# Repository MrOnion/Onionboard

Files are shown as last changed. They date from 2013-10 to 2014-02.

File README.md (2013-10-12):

# Onionboard PCB for FreeEMS

This PCB is intended to be used in conjunction with a separate microcontroller module to create a basic engine management system. It has a simple power supply and enough general purpose I/O to get started. Basically any microcontroller and software combo can be used but it is particulary designed to be used with the open-source FreeEMS project.

http://freeems.org/

Its ideal for people who wants to experiment and learn about the world of engine management.

The project is done with CadSoft Eagle version 6.x and is kept within the freeware limitations.

http://www.cadsoftusa.com/download-eagle/freeware/

## Features

* 2-Layer PCB
* Size is about 10x10cm (fits in a euro case)
* 5V LDO regulated power supply with VDR protection
* 2 Polyfuse protected 5V reference voltage outputs
* 4 auto-protected injector outputs (high impedance only)
* 2 auto-protected accessory outputs
* 4 mosfet drivers for ignition amplifiers (5V or 12V)
* 4 protected A/D inputs
* 4 protected temperature inputs (can be used as normal A/D)
* 2 protected on/off switch inputs
* 2 ground loop monitor inputs
* CEL LED and run/load switch for FreeEMS

One thing to point out is that at this stage the board DOES NOT have VR/Hall sensor inputs. As these sensors are mandatory to operate an EMS there are pin headers/DIP8 socket and places for shunt resistors (used with VR) to be used with a separate BrickRPM VR conditioner board. More info at: http://brickems.com/brickrpm/

## Notes

The schematic and board file both have a placeholder for git commit id. This is used with the git clean/smudge filter. The .gitattributes file is included with the project but it only defines the files to be filtered with a filter called "hasher". You can use this feature by adding this into your .git/config file:
```
[filter "hasher"]
        smudge = sed \"s/GIT %GIT_COMMIT_ID%/GIT `git rev-parse --verify HEAD --short`/\"
        clean = sed \"s/GIT [0-9a-z]\\{7\\}/GIT %GIT_COMMIT_ID%/\"
```
As you can see this is OS specific and works straight in Linux and OSX.

The filter has one downside which is the need to make an extra deletion and checkout for the id to be "smudged". For example if you clone this project the git placeholder don't have the current id. You need to delete the files and checkout them for the id to be updated:

```
$ rm onionboard.sch onionboard.brd 
$ git checkout onionboard.sch onionboard.brd
```

The project uses a separate Molex connector library I found here:
https://code.google.com/p/rdubniewski-test/source/browse/trunk/eagle.lib/con-molex-5569.lbr
It's also included in the libs directory.

If you decide to home etch this pcb I recommend to make the vias larger (the copper area) before doing so. This way its easier to drill them and solder the connecting wire.

Heres a good tip for home made vias:
http://www.youritronics.com/double-layer-pcb-home-made-vias/

## TODO

* Get more testing done and lots of driving/racing.
* Possibly put a dual VR conditioner on board (MAX992x based)
* Also one H-bridge driver would be ideal

## CPU Modules used with FreeEMS (MC9S12XDP512)

* **TA Adapt9S12XDP512** - http://www.technologicalarts.ca/shop/store/details/453/11/microcontrollers/adapt9s12xdp512m2-xgate-mcu-module,-full-configuration.html
* **ElMicro CardS12** - http://elmicro.com/en/cards12.html
* **WayEngineer MC9S12XDP512-core** - http://www.wayengineer.com/index.php?main_page=product_info&products_id=281

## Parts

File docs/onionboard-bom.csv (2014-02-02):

Qty | Value | Package | Parts | Description
1 |  | 1X02 | JP1 | Through-hole pin header (VR1/2 Out)
2 |  | 1X04 | JP6, JP7 | Through-hole pin header (BrickRPM)
48 |  | SMD1,27-2,54 | ACC1, ACC2, ACCMON, AD1, AD2, AD3, AD4, ADB1, ADB2, ADB3, ADB4, BRV, CEL+, CEL-, IGN1, IGN2, IGN3, IGN4, INJ1, INJ2, INJ3, INJ4, INJMON, LD_RUN1, LD_RUN2, PA6, PAD3, PAD4, PAD5, PAD6, PAD7, PAD8, PAD13, PAD14, PAD17, PAD18, PAD19, PAD20, PAD21, PAD22, PAD27, PAD28, PAD29, PAD30, PAD35, PAD36, SW1, SW2 | SMD pin headers (pin count)
4 | 1uF | C0805 | C1, C3, C5, C7 | CAPACITOR, A/D bias inputs
9 | 0.1uF | C0805 | C2, C4, C6, C8, C14, C16, C18, C20, C22 | CAPACITOR, A/D channels
2 | 0.1uF | C1206 | C11, C12 | CAPACITOR, Power supply
5 | 0.22uF | C0805 | C13, C15, C17, C19, C21 | CAPACITOR, A/D non-biased inputs
2 | 15nF | C0805 | C23, C24 | CAPACITOR, GND monitors
2 | 1uF | C1206 | C25, C26 | CAPACITOR, MOSFET drivers
1 | 10uF | SMC_E | C9 | POLARIZED CAPACITOR, Power supply
1 | 47uF | SMC_E | C10 | POLARIZED CAPACITOR, Power supply
2 | 5k | 411 | R6, R8 | RESISTOR, Shunt
4 | 100R | 411 | R52, R53, R54, R55 | RESISTOR, Current limit
11 | 470R | R1206 | R1, R3, R4, R5, R11, R13, R14, R15, R44, R50, R51 | RESISTOR, A/D channels
10 | 100k | M0805 | R22, R24, R26, R28, R30, R32, R37, R38, R39, R40 | RESISTOR, Output pulldown
13 | 1k | M0805 | R21, R23, R25, R27, R29, R31, R33, R34, R35, R36, R46, R47, R48 | RESISTOR, Output limit, BRV, CEL/Load
4 | 1k | R0805 | R9, R10, R56, R57 | RESISTOR, BrickRPM hall mod
4 | 1k | R1206 | R16, R18, R19, R20 | RESISTOR, Switch inputs
4 | 2.49k | M0805 | R2, R7, R12, R17 | RESISTOR, A/D Bias
1 | 3.9k | M0805 | R45 | RESISTOR, BRV
1 | 2.4k | M0805 | R49 | RESISTOR, CEL
1 | 5.1V | P1Z12 | D9 | Z-Diode, Power supply
2 | 4.7V | SOT23 | D13, D14 | Z-Diode, Switch inputs
13 | BAT54S | SOT23 | D1, D2, D3, D4, D5, D6, D7, D8, D10, D11, D12, D15, D16 | Schottky Diodes, A/D channels
1 | 22-27-2041-04 | 6410-04 | J1 | CONNECTOR Molex, Power supply
2 | 5569-6 | 5569-6 | X2, X3 | 4.20mm Pitch Mini-Fit Jr.™ - 6 pin
1 | 5569-8 | 5569-8 | X1 | 4.20mm Pitch Mini-Fit Jr.™ - 8 pin
1 | D0A-L | D02A-L | KK1 | HEATSINK
1 | LM2940 | 78XXL | IC3 | VOLTAGE REGULATOR
2 | RXE030 | RXE030 | R42, R43 | POLYFUSE, Vref outputs
1 | S14K11 | S14K11 | R41 | VARISTOR, Power supply
2 | TC442xA | SO08 | IC1, IC2 | Dual High-Speed Power MOSFET Drivers
6 | VND14NV04 | TO252 (DPAK) | Q1, Q2, Q3, Q4, Q5, Q6 | Fully autoprotected Power MOSFET

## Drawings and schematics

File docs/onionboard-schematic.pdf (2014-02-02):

### ABCDE

### ABCDE

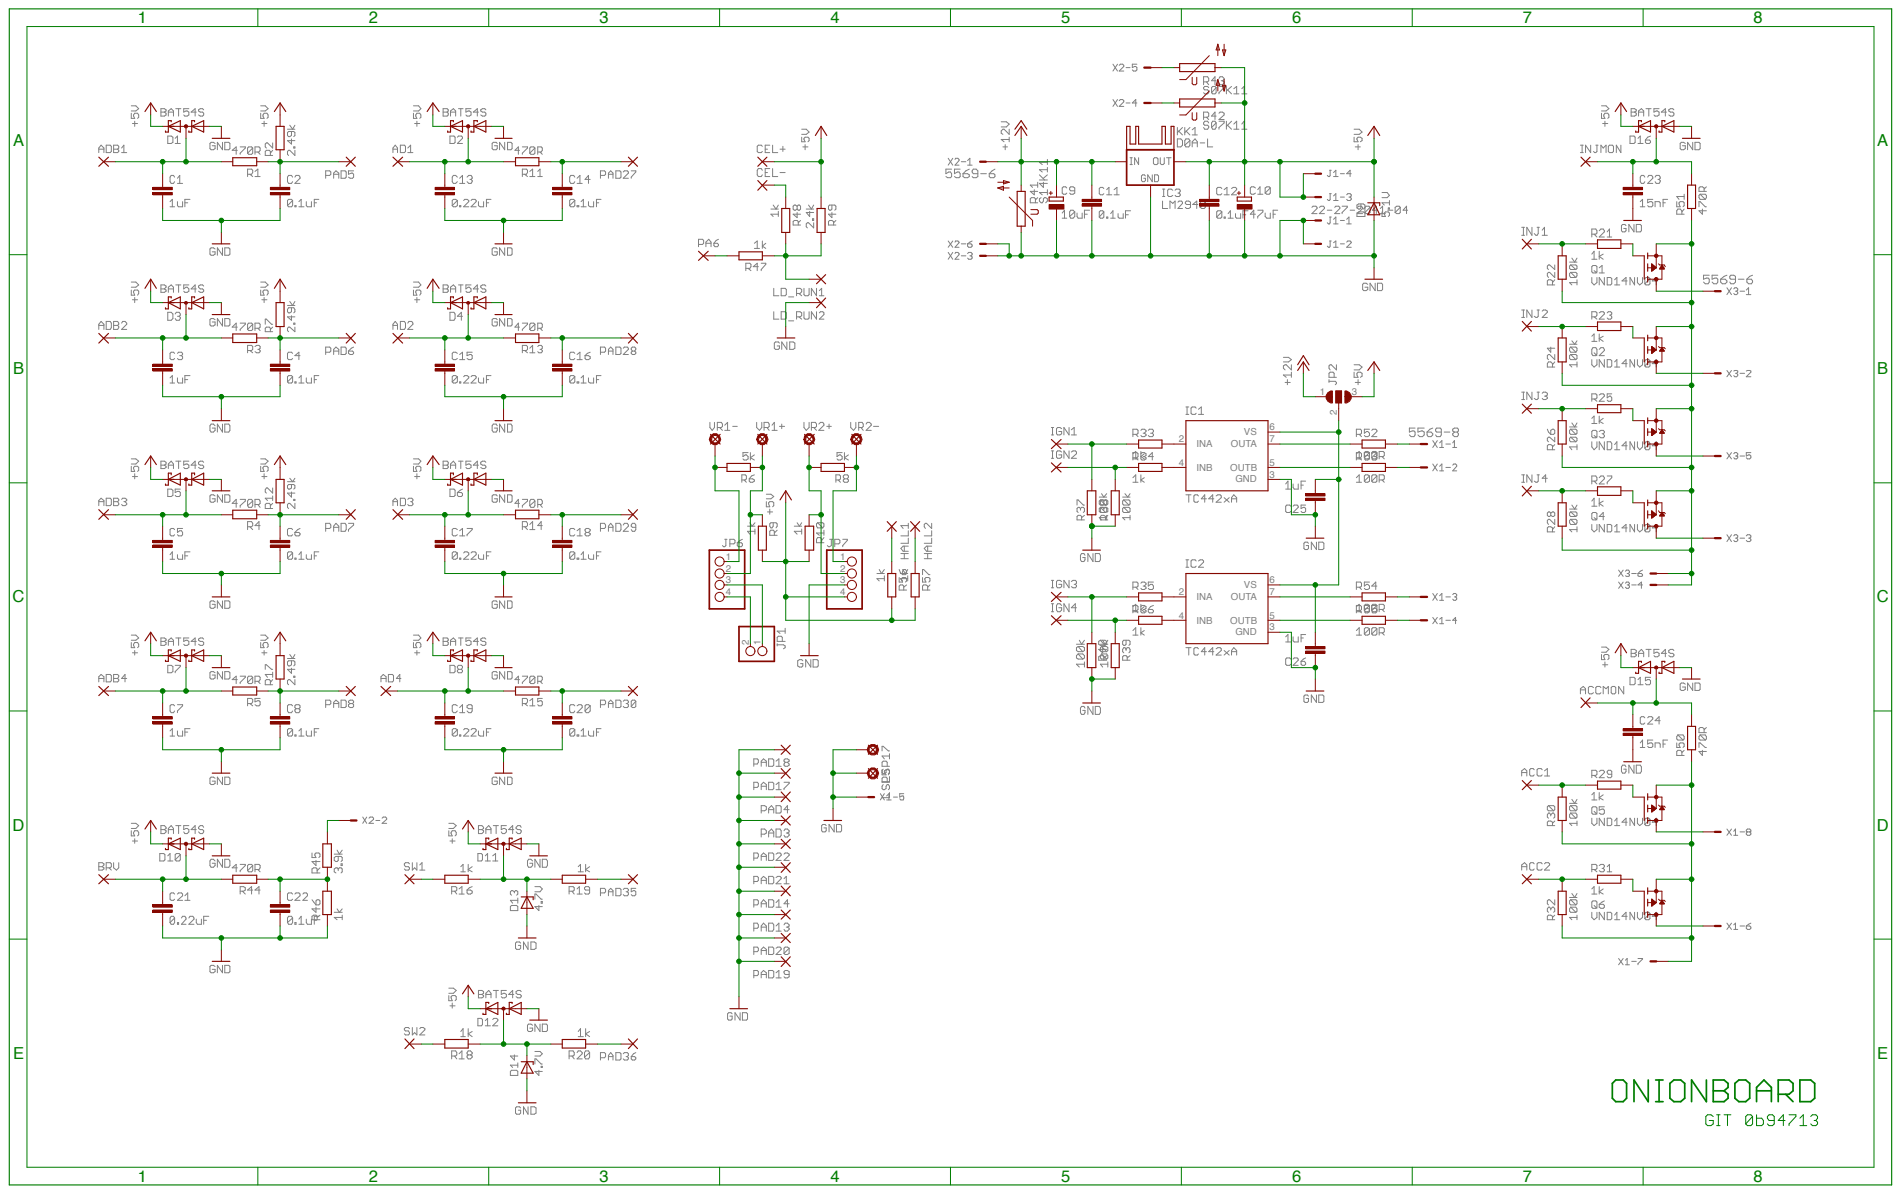
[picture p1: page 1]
INA; INB; OUTA; OUTB; GND

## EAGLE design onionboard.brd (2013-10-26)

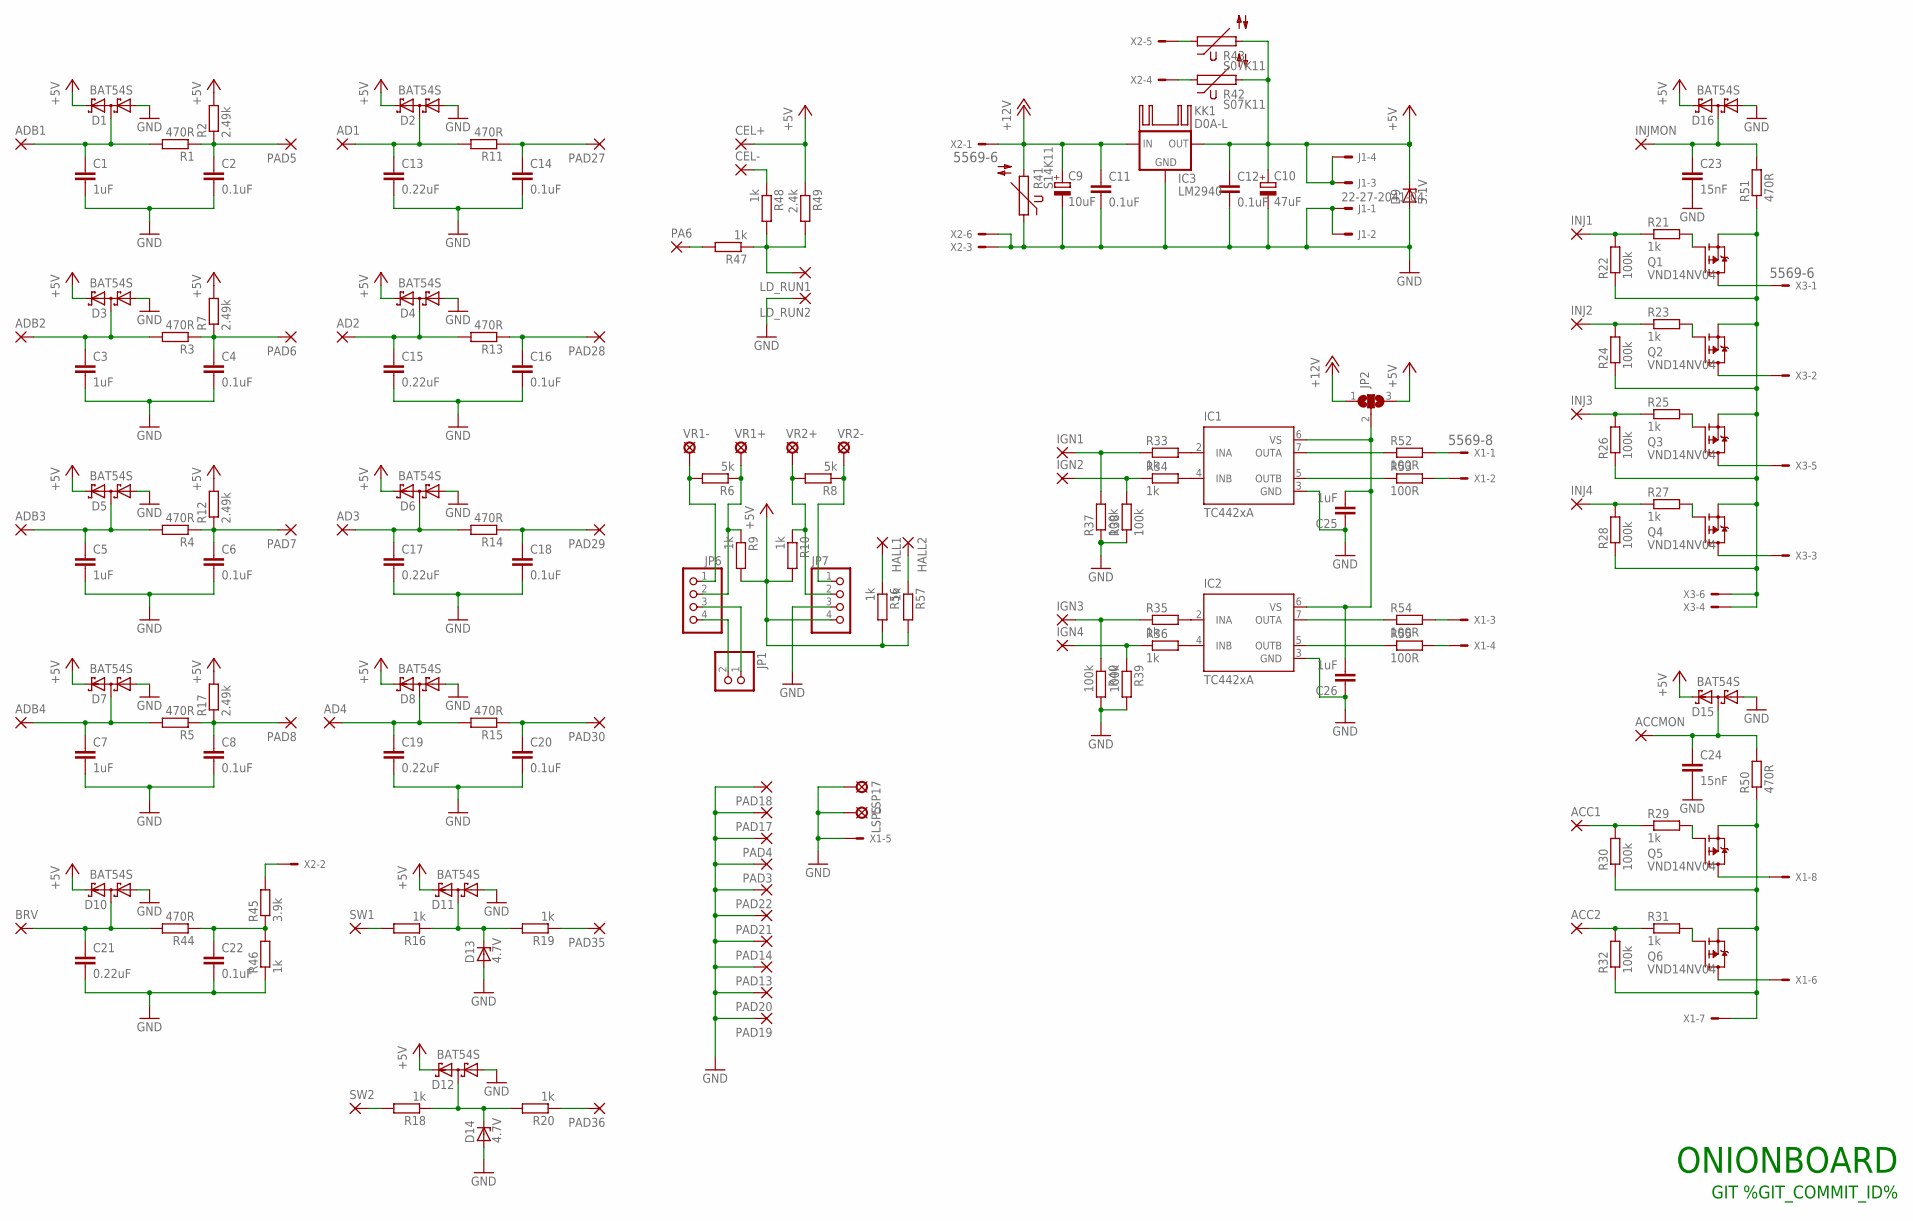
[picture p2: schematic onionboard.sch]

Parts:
ACC1, ACC2: SMD2; SMD1,27-2,54
ACCMON: SMD2; SMD1,27-2,54
AD1, AD2, AD3, AD4: SMD2; SMD1,27-2,54
ADB1, ADB2, ADB3, ADB4: SMD2; SMD1,27-2,54
BRV: SMD2; SMD1,27-2,54
C1, C3, C5, C7: 1uF; C0805
C2, C4, C6, C8, C14, C16, C18, C20, C22: 0.1uF; C0805
C9: 10uF; SMC_E
C10: 47uF; SMC_E
C11, C12: 0.1uF; C1206
C13, C15, C17, C19, C21: 0.22uF; C0805
C23, C24: 15nF; C0805
C25, C26: 1uF; C1206
CEL+: SMD2; SMD1,27-2,54
CEL-: SMD2; SMD1,27-2,54
D1, D2, D3, D4, D5, D6, D7, D8, D10, D11, D12, D15, D16: BAT54S; SOT23
D9: 5.1V; P1Z12
D13, D14: 4.7V; SOT23
HALL1, HALL2: 1,6/0,8
IC1, IC2: TC442xA; SO08
IC3: LM2940; 78XXL
IGN1, IGN2, IGN3, IGN4: SMD2; SMD1,27-2,54
INJ1, INJ2, INJ3, INJ4: SMD2; SMD1,27-2,54
INJMON: SMD2; SMD1,27-2,54
J1: 22-27-2041-04; 6410-04
JP1: PINHD-1X2; 1X02
JP2: SJ2W; SJ_2
JP6, JP7: PINHD-1X4; 1X04
KK1: D0A-L; D02A-L
LD_RUN1, LD_RUN2: SMD2; SMD1,27-2,54
LSP5, LSP17: LSP10
PA6: SMD2; SMD1,27-2,54
PAD3, PAD4, PAD5, PAD6, PAD7, PAD8, PAD13, PAD14, PAD17, PAD18, PAD19, PAD20, PAD21, PAD22, PAD27, PAD28, PAD29, PAD30, PAD35, PAD36: SMD2; SMD1,27-2,54
Q1, Q2, Q3, Q4, Q5, Q6: VND14NV04; TO252
R1, R3, R4, R5, R11, R13, R14, R15, R44, R50, R51: 470R; R1206
R2, R7, R12, R17: 2.49k; M0805
R6, R8: 5k; 0411/15
R9, R10, R56, R57: 1k; R0805
R16, R18, R19, R20: 1k; R1206
R21, R23, R25, R27, R29, R31, R33, R34, R35, R36, R46, R47, R48: 1k; M0805
R22, R24, R26, R28, R30, R32, R37, R38, R39, R40: 100k; M0805
R41: S14K11
R42, R43: S07K11
R45: 3.9k; M0805
R49: 2.4k; M0805
R52, R53, R54, R55: 100R; 0414V
SW1, SW2: SMD2; SMD1,27-2,54
VR1+, VR1-, VR2+, VR2-: LSP10
X1: 5569-8
X2, X3: 5569-6

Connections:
+5V: C10.+, C12.1, CEL+.1, D1.2 (C2), D2.2 (C2), D3.2 (C2), D4.2 (C2), D5.2 (C2), D6.2 (C2), D7.2 (C2), D8.2 (C2), D9.C, D10.2 (C2), D11.2 (C2), D12.2 (C2), D15.2 (C2), D16.2 (C2), IC3.OUT, J1.3, J1.4, JP2.3, JP7.4, R2.2, R7.2, R9.2, R10.2, R12.2, R17.2, R42.2, R43.2, R49.1, R56.2, R57.2
+12V: C9.+, C11.1, IC3.IN, JP2.1, R41.2, X2.1
GND: C1.2, C2.2, C3.2, C4.2, C5.2, C6.2, C7.2, C8.2, C9.-, C10.-, C11.2, C12.2, C13.2, C14.2, C15.2, C16.2, C17.2, C18.2, C19.2, C20.2, C21.2, C22.2, C23.2, C24.2, C25.1, C26.1, D1.1 (A1), D2.1 (A1), D3.1 (A1), D4.1 (A1), D5.1 (A1), D6.1 (A1), D7.1 (A1), D8.1 (A1), D9.A, D10.1 (A1), D11.1 (A1), D12.1 (A1), D13.1 (A), D14.1 (A), D15.1 (A1), D16.1 (A1), IC1.3 (GND), IC2.3 (GND), IC3.GND, J1.1, J1.2, JP7.3, LD_RUN2.1, LSP5.MP, LSP17.MP, PAD3.1, PAD4.1, PAD13.1, PAD14.1, PAD17.1, PAD18.1, PAD19.1, PAD20.1, PAD21.1, PAD22.1, R37.1, R38.1, R39.2, R40.2, R41.1, R46.1, X1.5, X2.3, X2.6
GNDAUX: Q5.2 (S), Q6.2 (S), R30.1, R32.1, R50.1, X1.7
GNDINJ: Q1.2 (S), Q2.2 (S), Q3.2 (S), Q4.2 (S), R22.1, R24.1, R26.1, R28.1, R51.1, X3.4, X3.6
IGNVCC: C25.2, C26.2, IC1.6 (VS), IC2.6 (VS), JP2.2
unnamed: C2.1, PAD5.1, R1.1, R2.1
unnamed: C14.1, PAD27.1, R11.1
unnamed: AD1.1, C13.1, D2.3 (C1A2), R11.2
unnamed: AD2.1, C15.1, D4.3 (C1A2), R13.2
unnamed: C16.1, PAD28.1, R13.1
unnamed: ADB1.1, C1.1, D1.3 (C1A2), R1.2
unnamed: Q6.3 (D), X1.6
unnamed: ADB2.1, C3.1, D3.3 (C1A2), R3.2
unnamed: C4.1, PAD6.1, R3.1, R7.1
unnamed: C18.1, PAD29.1, R14.1
unnamed: AD3.1, C17.1, D6.3 (C1A2), R14.2
unnamed: IGN1.1, R33.1, R37.2
unnamed: AD4.1, C19.1, D8.3 (C1A2), R15.2
unnamed: IGN2.1, R34.1, R38.2
unnamed: C20.1, PAD30.1, R15.1
unnamed: ADB3.1, C5.1, D5.3 (C1A2), R4.2
unnamed: ADB4.1, C7.1, D7.3 (C1A2), R5.2
unnamed: C6.1, PAD7.1, R4.1, R12.1
unnamed: PA6.1, R47.2
unnamed: IGN3.1, R35.1, R40.1
unnamed: IGN4.1, R36.1, R39.1
unnamed: IC1.7 (OUTA), R52.1
unnamed: IC2.5 (OUTB), R55.1
unnamed: C8.1, PAD8.1, R5.1, R17.1
unnamed: JP6.1, R6.2, VR1-.MP
unnamed: IC1.5 (OUTB), R53.1
unnamed: IC2.7 (OUTA), R54.1
unnamed: JP6.2, R6.1, R9.1, VR1+.MP
unnamed: JP7.2, R8.2, R10.1, VR2+.MP
unnamed: JP7.1, R8.1, VR2-.MP
unnamed: ACCMON.1, C24.1, D15.3 (C1A2), R50.2
unnamed: C23.1, D16.3 (C1A2), INJMON.1, R51.2
unnamed: ACC1.1, R29.1, R30.2
unnamed: Q5.3 (D), X1.8
unnamed: INJ1.1, R21.1, R22.2
unnamed: INJ2.1, R23.1, R24.2
unnamed: INJ3.1, R25.1, R26.2
unnamed: INJ4.1, R27.1, R28.2
unnamed: IC1.2 (INA), R33.2
unnamed: IC1.4 (INB), R34.2
unnamed: IC2.4 (INB), R36.2
unnamed: IC2.2 (INA), R35.2
unnamed: R45.2, X2.2
unnamed: JP1.1, JP6.3
unnamed: R52.2, X1.1
unnamed: R43.1, X2.5
unnamed: R42.1, X2.4
unnamed: ACC2.1, R31.1, R32.2
unnamed: R53.2, X1.2
unnamed: R54.2, X1.3
unnamed: JP1.2, JP6.4
unnamed: D11.3 (C1A2), D13.3 (C), R16.1, R19.2
unnamed: PAD36.1, R20.1
unnamed: D12.3 (C1A2), D14.3 (C), R18.1, R20.2
unnamed: Q2.1 (G), R23.2
unnamed: Q3.1 (G), R25.2
unnamed: Q4.1 (G), R27.2
unnamed: Q5.1 (G), R29.2
unnamed: Q6.1 (G), R31.2
unnamed: Q1.1 (G), R21.2
unnamed: BRV.1, C21.1, D10.3 (C1A2), R44.2
unnamed: C22.1, R44.1, R45.1, R46.2
unnamed: R55.2, X1.4
unnamed: HALL2.1, R57.1
unnamed: R16.2, SW1.1
unnamed: PAD35.1, R19.1
unnamed: R18.2, SW2.1
unnamed: HALL1.1, R56.1
unnamed: Q4.3 (D), X3.3
unnamed: LD_RUN1.1, R47.1, R48.2, R49.2
unnamed: Q3.3 (D), X3.5
unnamed: Q2.3 (D), X3.2
unnamed: Q1.3 (D), X3.1
unnamed: CEL-.1, R48.1

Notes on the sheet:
ONIONBOARD
GIT %GIT_COMMIT_ID%

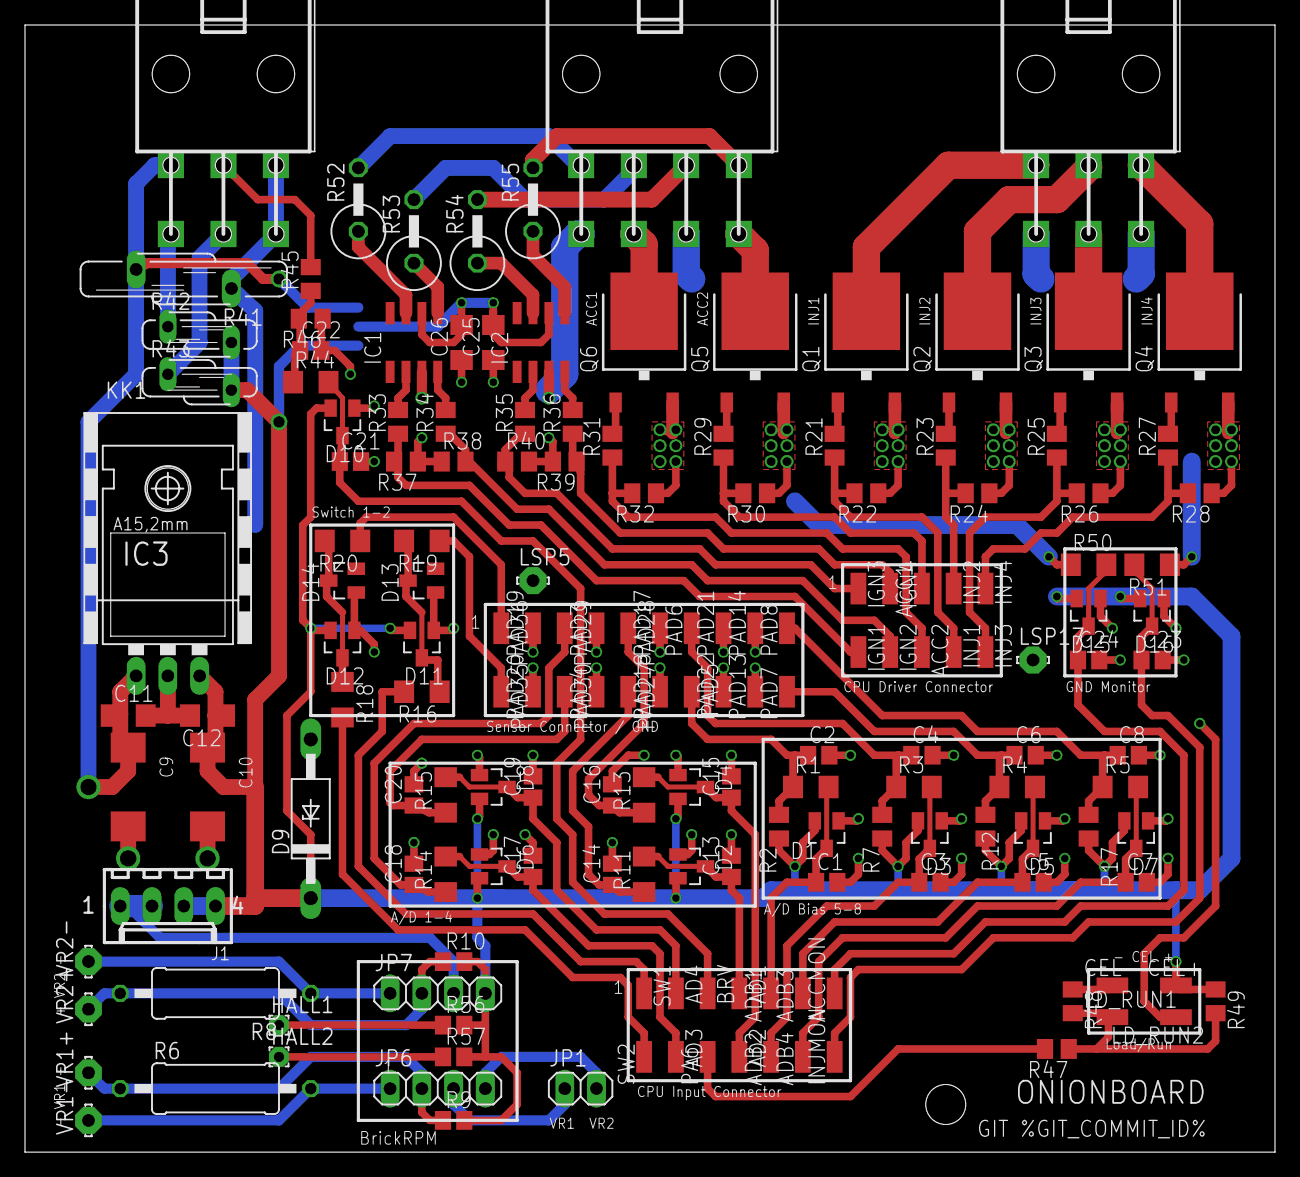
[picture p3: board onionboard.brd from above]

Board: 4 copper layers, 100.0 x 90.2 mm, 173 parts (1 on the bottom side), 80 nets.

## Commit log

2013-10-10 Cleaned up and rearranged the schematic. Moved two ground vias on monitor schottkys
    [onionboard.brd, onionboard.sch]
2013-10-11 more schematic clean up
    [onionboard.sch]
2013-10-12 Even more schematic refactor and added values to components. Added silkscreen for molex connectors
    [onionboard.brd, onionboard.sch]
2013-10-12 Added git commit id to schematic and added the filter into gitattributes. Also updated README with the commit id filter info
    [onionboard.sch]
2013-10-26 Changed VDR/MOV size from 20mm to 14mm. Moved powersupply section a bit lower to fit the heatsink properly
    [onionboard.brd, onionboard.sch]
2014-02-02 Added BOM and schematic PDF to docs
    [onionboard-bom.csv]
